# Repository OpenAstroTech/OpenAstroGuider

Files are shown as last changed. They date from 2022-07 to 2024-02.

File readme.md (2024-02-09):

# OpenAstroGuider v3.1
OAGv3

## Additions in v3.1
- Custom PCB for easier wiring and USB-C connector
- slightly adjusted front and rear parts for easier mounting to OAT
- larger channel for dew heater cable

## Additions in v3.0
- (optional) Build in dew heater powered directly from USB power
- Sturdier build
- Sturdier holders
- Better focuser
- Light baffles against internal reflections
- Strain relief for IMX USB cable

OAGv3 Cross Section

## Required parts

TODO Google sheet part chooser
Wiki hardware

#### Screws & Nuts
- 2x M3x8mm 
- 2x M3x12mm
- 8x M3x20mm
- 8x M3 Hex Nut
- 4x M3x4.6x6mm Heatsert
- 4x M4x12mm
- 4x M4 TNut
- (optional) 1x M3x12 Thumbscrew

#### Other
- IMX290 camera module + USB Cable
- 183/50mm achromatic lens
- about 200g of dark filament
- (Vixen mount) 1x 2020x200mm extrusion

--- 

<br /> <a href="https://github.com/OpenAstroTech/OpenAstroGuider"> OpenAstroGuider </a> &copy; 2023 by <a href="https://github.com/OpenAstroTech">OpenAstroTech </a> is licenced under <a rel="license" href="http://creativecommons.org/licenses/by-nc/4.0/">CC BY-NC 4.0</a>.

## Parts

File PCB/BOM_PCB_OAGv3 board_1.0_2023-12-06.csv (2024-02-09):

ID | Name | Designator | Footprint | Quantity | Manufacturer Part | Manufacturer | Supplier | Supplier Part | Price
1 | XH-2AW_C2908611 | HEATER,SWITCH | CONN-TH_XH-2AW_C2908611 | 2 |  | HCTL(华灿天禄) | LCSC | C2908611 | 0.006
2 | PH-4AW_C722777 | IMX | CONN-TH_PH-4AW_C722777 | 1 |  | CAX | LCSC | C722777 | 0.009
3 | 918-468K2029E50001 | USBC | USB-C-TH_918-468K2029E50001 | 1 | 918-468K2029E50001 | 精拓金 | LCSC | C709026 | 0.589

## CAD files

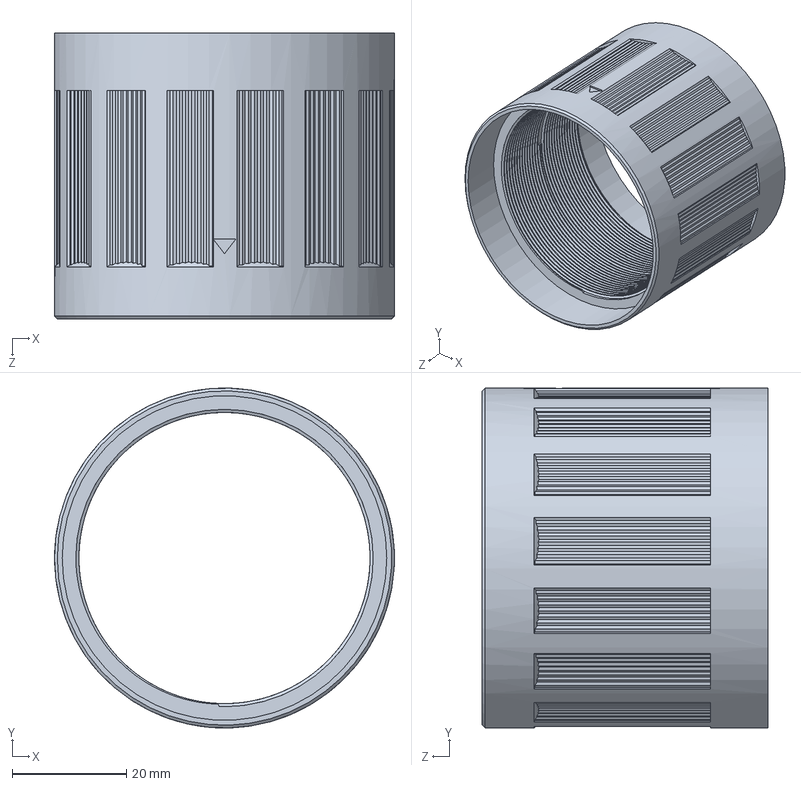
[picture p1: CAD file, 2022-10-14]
CAD/Solidworks/mid.SLDPRT
59.5 x 59.5 x 50.0 mm

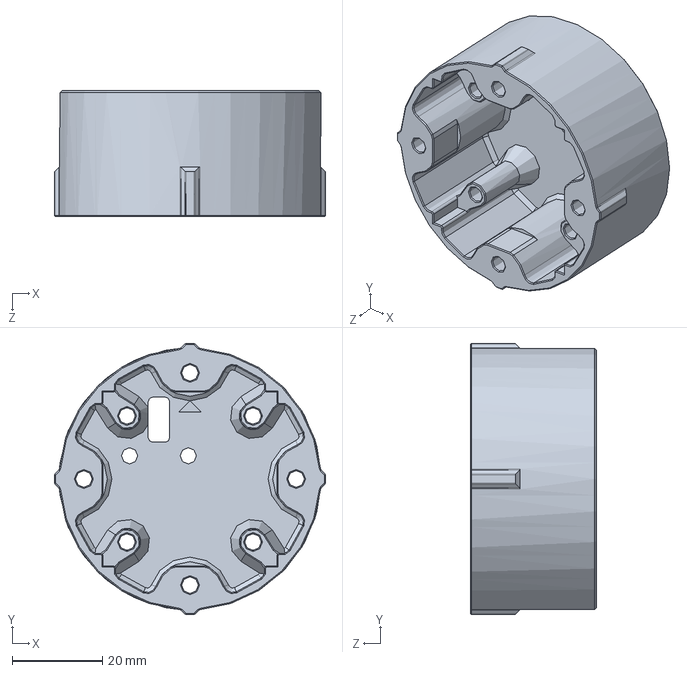
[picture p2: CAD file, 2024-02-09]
CAD/Solidworks/noPCB/Lid_cameraMount.SLDPRT
60.0 x 60.0 x 28.0 mm

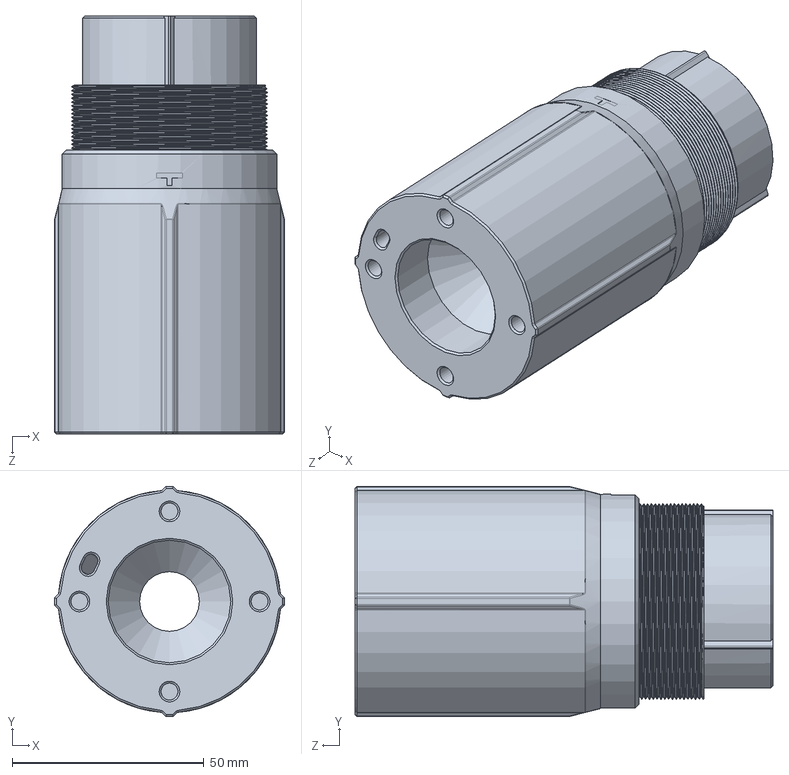
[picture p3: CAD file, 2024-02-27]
CAD/Solidworks/parts/rear_163mm.SLDPRT
60.0 x 60.0 x 109.0 mm

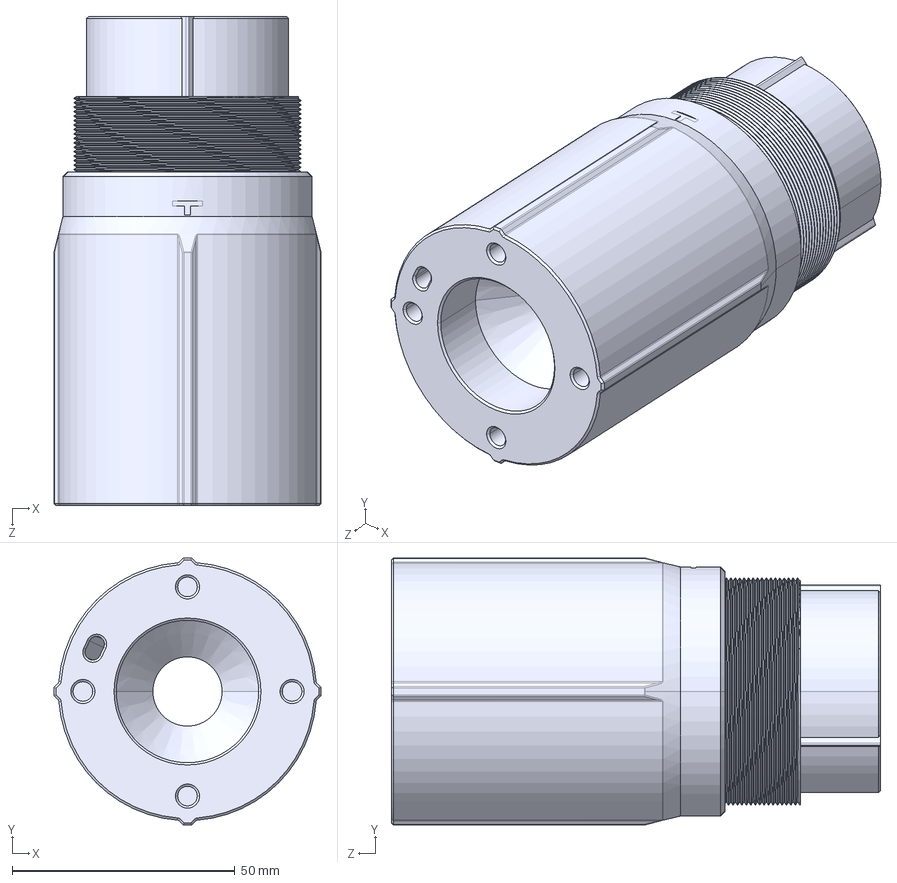
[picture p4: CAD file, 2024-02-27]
CAD/STEP/rear_183mm.STEP
60.0 x 60.0 x 110.0 mm

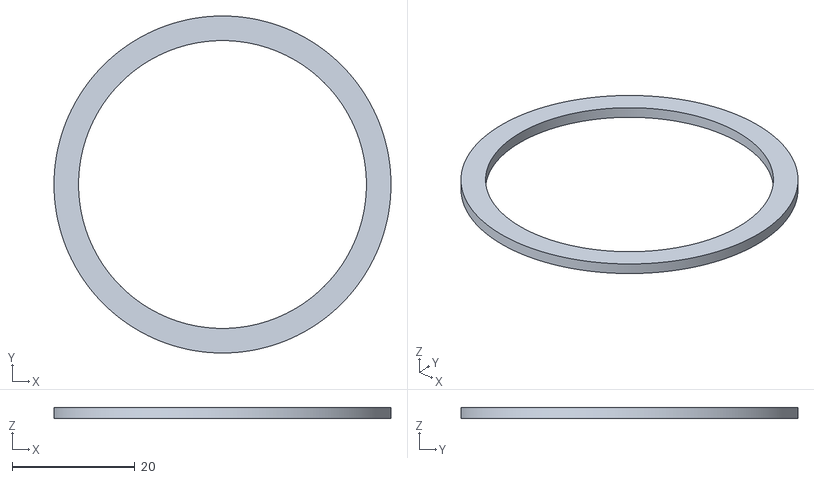
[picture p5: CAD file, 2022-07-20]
STL/DIY_resistor_heater/Resistor_distancer.STL
54.8 x 54.8 x 1.80

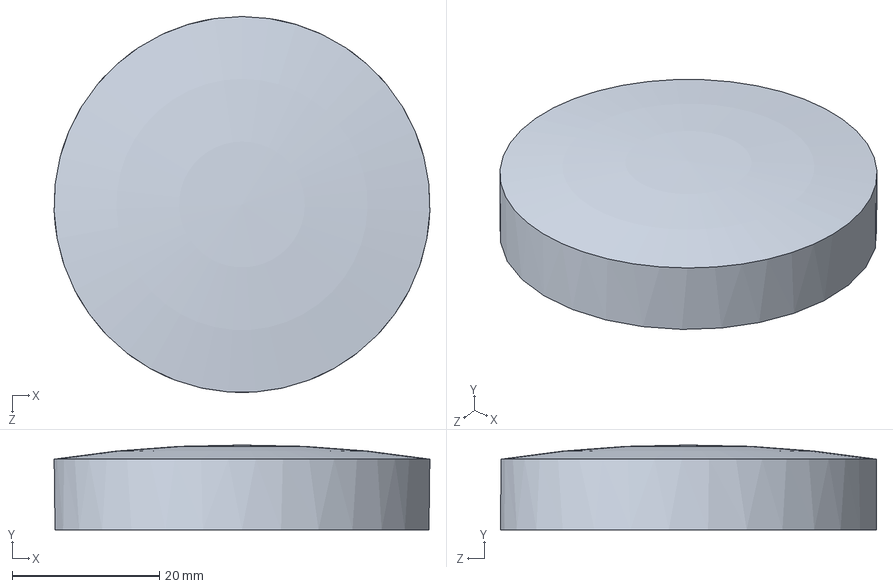
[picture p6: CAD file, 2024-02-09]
CAD/Solidworks/assembly/50.183 Linse.SLDPRT
51.0 x 11.5 x 51.0 mm

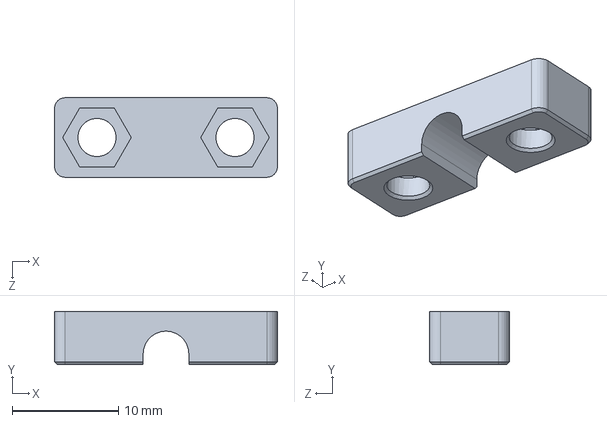
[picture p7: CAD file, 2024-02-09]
CAD/Solidworks/noPCB/Cable_strain_relief.SLDPRT
21.0 x 5.00 x 7.50 mm

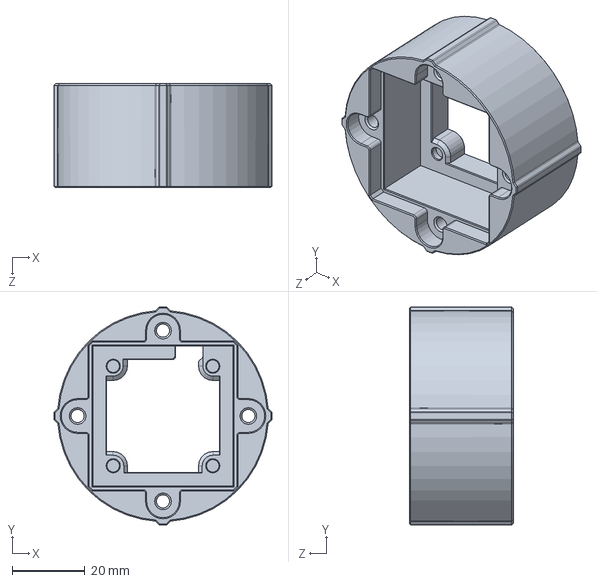
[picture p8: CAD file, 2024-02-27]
CAD/Solidworks/parts/cameraMount_v3.1.SLDPRT
60.0 x 60.0 x 28.6 mm

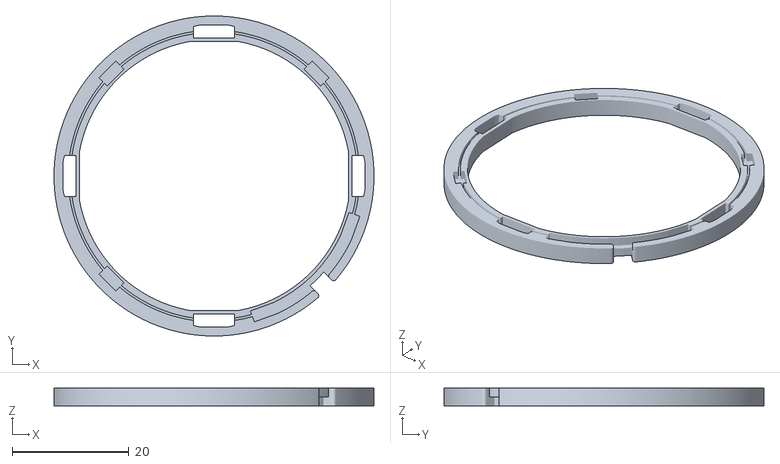
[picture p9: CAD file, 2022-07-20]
STL/DIY_resistor_heater/resistor_holder.STL
54.8 x 54.8 x 3.00

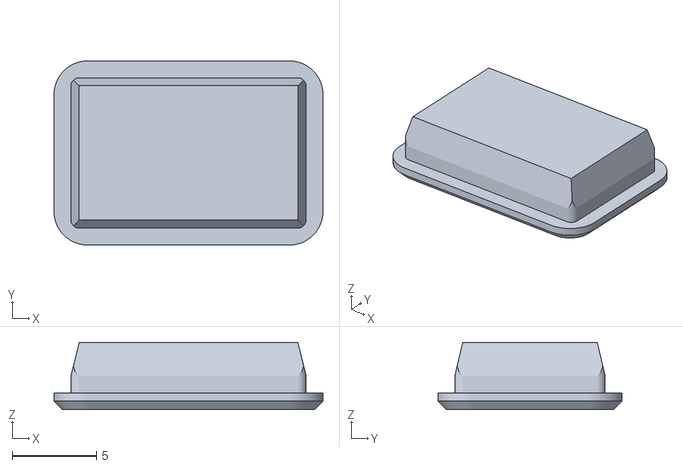
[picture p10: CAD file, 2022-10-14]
STL/noPCB, v3.0 parts/Switchhole_plug.STL
16.0 x 10.9 x 4.00

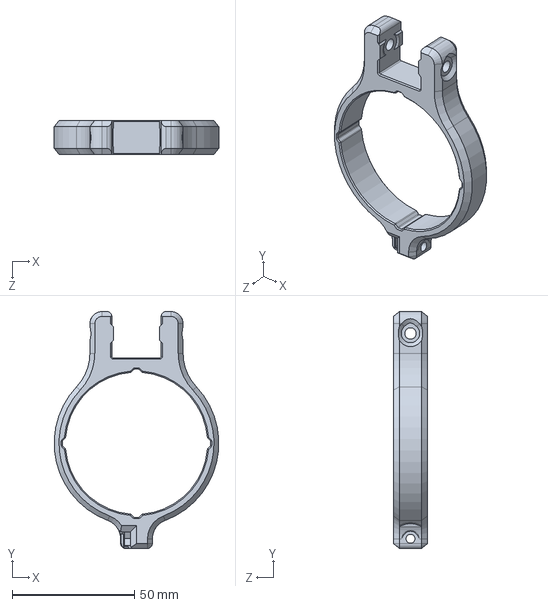
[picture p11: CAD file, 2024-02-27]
CAD/Solidworks/parts/holder_parent.SLDPRT
67.4 x 97.1 x 14.0 mm

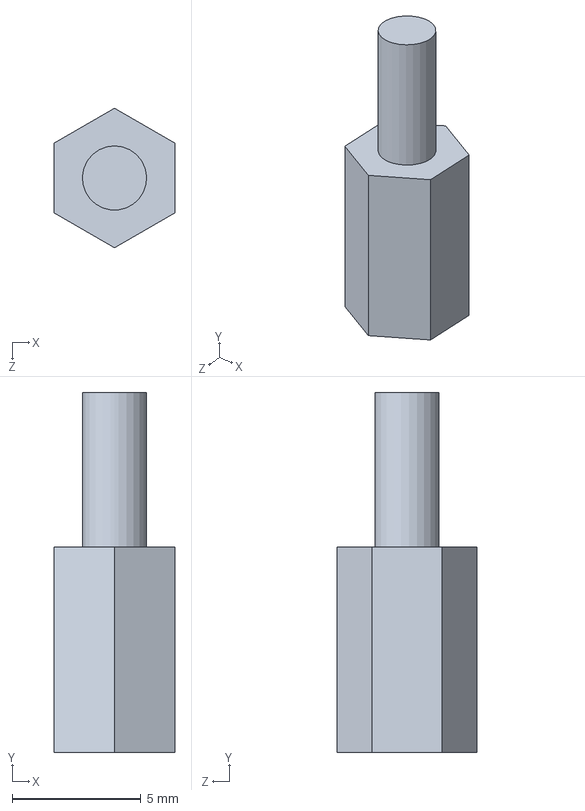
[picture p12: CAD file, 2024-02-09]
CAD/Solidworks/assembly/Distancer_M2.5_8mm.SLDPRT
4.70 x 14.0 x 5.43 mm

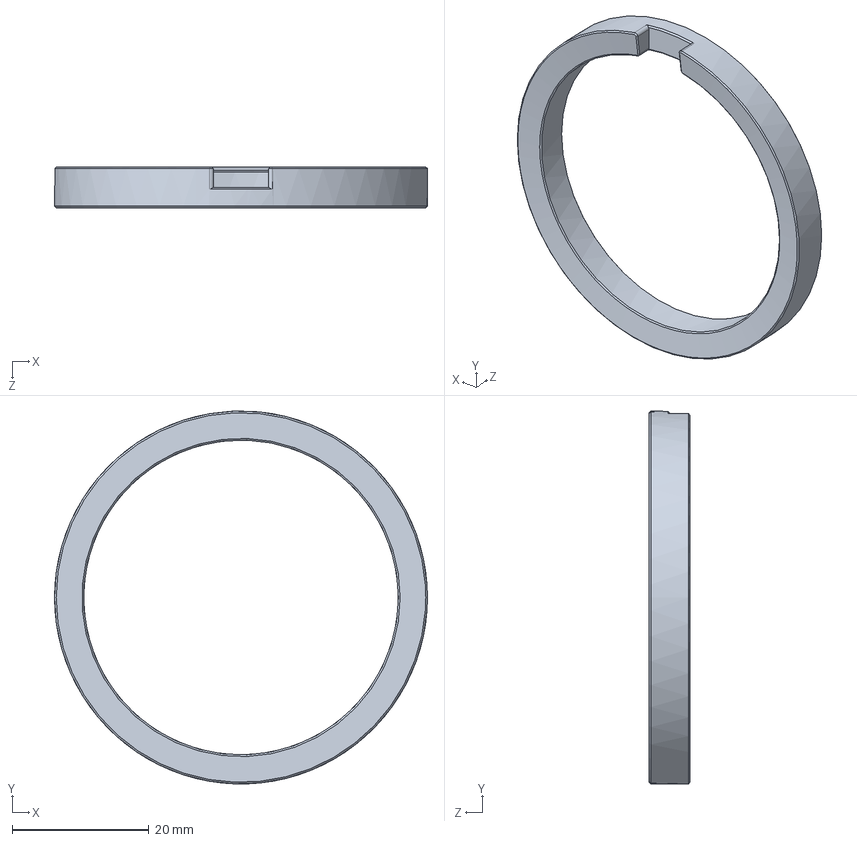
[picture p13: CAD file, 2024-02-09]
CAD/Solidworks/parts/Lens_holder.SLDPRT
54.5 x 54.5 x 5.96 mm

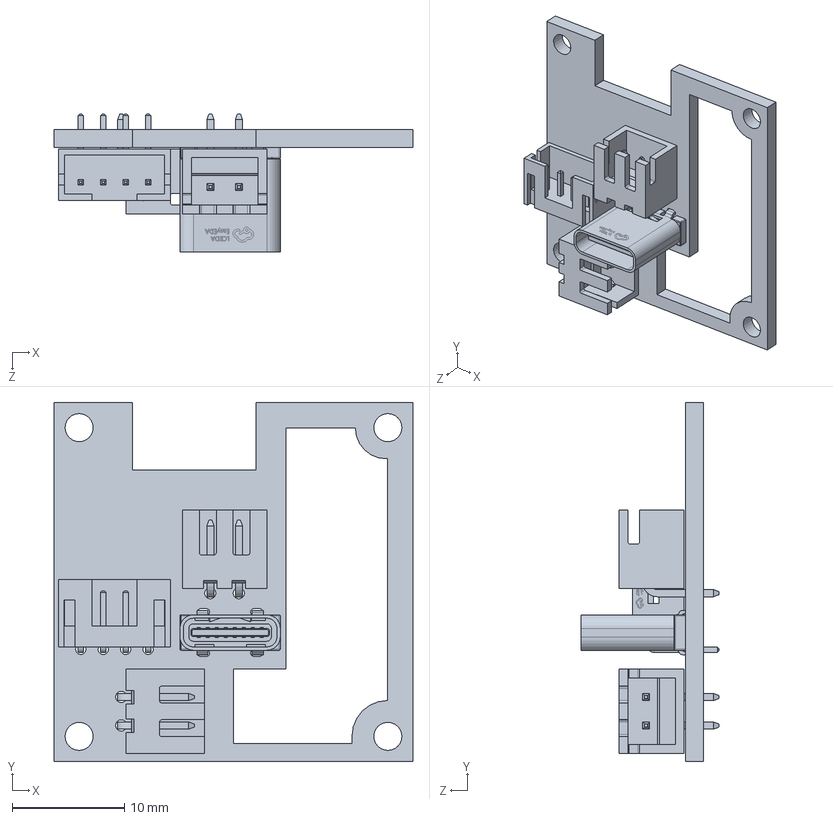
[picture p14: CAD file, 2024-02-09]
CAD/Solidworks/assembly/3D_PCB_OAGv3 board_0.9.SLDPRT
32.0 x 32.0 x 12.3 mm

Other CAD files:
STL/noPCB, v3.0 parts/Lid_cameraMount_noSwitch.STL
CAD/Solidworks/noPCB/Switchhole_plug.SLDPRT
STL/noPCB, v3.0 parts/Lid_cameraMount.STL
STL/noPCB, v3.0 parts/Lid_cameraMount_M2.STL
CAD/Solidworks/assembly/IMX290.SLDPRT
CAD/Solidworks/assembly/M3_nut.SLDPRT
CAD/Solidworks/assembly/M3x12.SLDPRT
CAD/Solidworks/assembly/M3x12_thumbscrew.SLDPRT
CAD/Solidworks/assembly/M3x20.SLDPRT
CAD/Solidworks/assembly/M3x6.SLDPRT
CAD/Solidworks/assembly/M4x12+TNut.SLDASM
CAD/Solidworks/assembly/M4x12.SLDPRT
CAD/Solidworks/assembly/T-Nut M4 20 Series.SLDPRT
CAD/Solidworks/assembly/alux20x20.SLDPRT
CAD/Solidworks/assembly/light path.SLDPRT
CAD/Solidworks/assembly/rocker_switch_10x15mm.SLDPRT
CAD/Solidworks/parts/Dew_Shield.SLDPRT
CAD/Solidworks/parts/Resistor_distancer.SLDPRT
CAD/Solidworks/parts/Vixen_adapter.SLDPRT
CAD/Solidworks/parts/cameraMount_lid.SLDPRT
CAD/Solidworks/parts/front.SLDPRT
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

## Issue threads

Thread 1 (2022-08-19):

"mid" scew to wide

Viper-Gtr, 2022-08-19:
the printed middle screw don't grab on the threads. Even in CAD the screw ist floating.

I printed the mid.part with -0.5mm in x and y to fit over the threads, but that didn't work either.
At the moment the oversized nut ist used and its focused over the holders.

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

GeneralSyb, 2022-09-19:
[mid v3.zip](https://github.com/OpenAstroTech/OpenAstroGuider/files/9601022/mid.v3.zip)

This ended up working for me.

Diameter of 58.55 mm. Printed it at **0.06 mm layer height** using a 0.4 mm nozzle, sliced in Cura for the ultimaker s2+, using black PLA PRO from REAL filament.
The layer height is **VERY** important. I recommend first just taking a small slice of the whole thing to test what diameter works best for you, because shrinkage can vary a lot depending on the printer and filament.

GeneralSyb, 2022-10-05:
Shrinkage with resin is very different with resin. My version might not
work for you. Layer height isn't a problem with resin like you said.

Op wo 5 okt. 2022 10:46 schreef Viper-Gtr ***@***.***>:

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

GeneralSyb, 2023-11-18:
That one did thread for me, but not properly. With a tiny but of force it
could just be lifted out. It also couldn't be tightened enough to really
lock the lens it place, so it wobbled a bit sometimes.
I ended up just buying a normal guide scope and camera. I didn't want to
mess around with this thing anymore.

Op za 18 nov. 2023 03:23 schreef Kyle ***@***.***>:

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

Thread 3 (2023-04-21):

Test STLs arent the same as the current parts

fail-open, 2023-04-21:
I should have noticed the commit messages being different between the test parts (v5) and the real parts (v6), but my test pieces meshed very nicely. I have not tired the front and back prints, but the test thread in the middle piece is a much different fit than the two test pieces. Mid piece feels much larger so the inner thread slides out.

Makes testing not as helpful.

daniel-gallagher, 2023-05-01:
I had the same experience. Test print middle threads were just about perfect. After printing the complete parts, I found that the middle section was far too large. I reprinted using the -1mm middle, but it is still a bit loose. I will try the -2mm middle next to see if that will be the right fit.

freiform, 2023-10-31:
I had to shrink the -0.2mm middle by another 0.3mm in x and y to have the threads engaging properly.

I would recommend ditching the test STLs for now and just print the front and back and then print about 10 mm of the focusing ring's ('middle') thread. In the slicer
- move the part into the bed so it gets cut so you just get the thread
- use cut (in e.g. PrusaSlicer) at a height of 7-10mm or just abort the print at that height, e.g. with Cura (couldn't find an appropriate funcion there).
- Try on the 'rear' part and resize in Slicer if needed.

For me, it was okayish on the bottom part but way too loose on the front, but that may be my cheap printer, so YMMV. If you want to try out the fit for the front part, just rotate the middle by 180° in x or y and print a section of thread as described above.

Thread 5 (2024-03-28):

Which 3.1 focuser/mid do i print?

kfechter, 2024-03-28:
kind of a dumb question, but I'm at a loss here. I have all the 3.1 files I think I need to print except the mid, focuser. however there are 10 different mid files with different mm values, and im not finding any docs that tell me which one i need to print.

Clay2F, 2024-03-28:
There is a test print file to find the right tolerance for the mid part.
the test that fits best is the part which you should youse for the final print

kfechter, 2024-03-28:
got it, thanks! i'll close this issue

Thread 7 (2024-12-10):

Instructions missing

co2e14, 2024-12-10:
Could we have some instructions added to this project?

What heater?
What custom PCB?
How to install heater?
What does TI/noTI mean in the file name?

Trigger-broom-289, 2024-12-10:
Hello,

_What heater / PCB_
https://shop.openastrotech.com/collections/openastroguider/products/openastroguider-hardware-only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

_How to install heater?_
https://wiki.openastrotech.com/en/OpenAstroGuider/OpenAstroGuiderV3_DewHeater

_TI/noTI_
TI stands for Threaded Insert

Closed 2024-12-11.

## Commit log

2022-07-15 Add current Solidworks parts
    Version 3.0.0-beta
    [50.183 Linse.SLDPRT, Cable_strain_relief.SLDPRT, Dew_Shield.SLDPRT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]
2022-07-16 v3_beta002
    - added cable channel for dew heater
    - merged camera_mount and Lid into one part. Reduces light leaks
    - longer thread for dew shield
    - slightly beefed up holder mounts
    - removed resistor holder for now
    [50.183 Linse.SLDPRT, Cable_strain_relief.SLDPRT, Cable_strain_relief.STL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]
2022-07-16 v3_beta003
    - made some parts slightly more efficient to print
    [Dew_Shield.SLDPRT, Dew_Shield.STL, OpenAstroGuider_v3_beta002.SLDASM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]
2022-07-17 v3_rc1
    - add rear lid option for no switch
    [Lid_cameraMount.SLDPRT, Lid_cameraMount_noSwitch.STL, OpenAstroGuider_v3_beta003.SLDASM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]
2022-07-17 v3_rc2
    - minor fix for focus position
    [Dew_Shield.SLDPRT, Lid_cameraMount.SLDPRT, Lid_cameraMount.STL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]
2022-07-17 v3_rc2
    - add a small indicator for correct positioning of the IMX sensor
    [Lid_cameraMount.SLDPRT, Lid_cameraMount.STL, Lid_cameraMount_noSwitch.STL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]
2022-07-19 v3_rc2
    - minor adjustments to the holders
    [OpenAstroGuider_v3_rc2.SLDASM, holder_1.SLDPRT, holder_1.STL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]
2022-07-20 v3_rc3
    - minor adjustment to the holders diameter
    [OpenAstroGuider_v3_rc2.SLDASM, OpenAstroGuider_v3_rc3.SLDASM, front.SLDPRT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]
2022-07-20 add .step
    [Lid_cameraMount.SLDPRT, OpenAstroGuider_v3_rc3.SLDASM, alux20x20.SLDPRT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]
2022-07-20 v3_rc3
    - added TI and noTI versions for rear. (Threaded Inserts)
    - added resistor holder and spacer
    [50.183 Linse.SLDPRT, OpenAstroGuider_v3_rc3.SLDASM, Resistor_distancer.SLDPRT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]
2022-07-21 v3_rc4
    - added blunt threads
    - new lens cap
    [Cable_strain_relief.SLDPRT, Dew_Shield.SLDPRT, OpenAstroGuider_v3_rc3.SLDASM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]
2022-10-01 v3_rc5
    - adjusted thread tolerances of mid and dew shield
    - added test prints for focus thread
    [Dew_Shield.SLDPRT, Lens_holder.SLDPRT, Lens_holder.STL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]
2022-11-24 v3_rc6
    - add smaller mid pieces
    - add vixen adapter
    [OpenAstroGuider_v3_rc6.SLDASM, Vixen_adapter.SLDPRT, Vixen_adapter.STL]
2023-04-04 add 163mm version
2023-11-29 v3.1 reupload
    Update all parts to v3.1 compatible
    [3D_PCB_OAGv3 board_0.9.SLDPRT, 50.183 Linse.SLDPRT, Cable_strain_relief.SLDPRT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]
2023-11-29 update STLs
    [Cable_strain_relief.STL, Lid_cameraMount.STL, Lid_cameraMount_M2.STL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]
2023-12-06 adjust dew shield fit
    [Dew_Shield.SLDPRT, Dew_Shield.STL]
2023-12-06 new test prints
    [mid.SLDPRT]
2023-12-06 add PCB files
    [BOM_PCB_OAGv3 board_1.0_2023-12-06.csv, PickAndPlace_PCB_OAGv3 board_1.0_2023-12-06.csv]
2024-01-13 updates
    slight tolerance adjustment for front thread and location of focus markers
    [Cable_strain_relief.STL, Lid_cameraMount.STL, Lid_cameraMount_M2.STL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]
2024-01-13 dew shield
    adjust dew shield thread length
    [Dew_Shield.SLDPRT, Dew_Shield.STL]
2024-02-27 minor adjustment
    slightly adjusted camera mount part to allow JST-2 to be inserted with the camera in place
    [cameraMount_v3.1.SLDPRT, holder_parent.SLDPRT, rear_163mm.SLDPRT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]
